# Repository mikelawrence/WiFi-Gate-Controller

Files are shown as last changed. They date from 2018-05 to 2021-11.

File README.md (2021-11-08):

# Wireless Gate Controller
After years of using weak garage door openers and trying to position them just right so my solar powered gate 400' away would open when needed I decided it was time to make a wireless controller of my own. 802.11 is a ubiquitous choice and with the right antenna range is not a problem. Two wireless modules consistently popped up when searching for low power embedded WiFi, ESP8266 and ATWINC1500. In the end I chose the ATWINC1500 module for it's compatibility with Arduino and it's low power modes. This board is fully compatible with the Arduino MRK1000 which includes a SAMD21G18 Arm processor and the ATWINC1500 module. I also chose to use MQTT. Recent projects showed how effective the MQTT client/server model is in this situation. I use Home Assistant for home automation and it directly supports MQTT.

This board is designed for and tested with a US Automation Gate Opener.

This PCB design uses my custom libraries available here [Mike's KiCad Libraries](https://github.com/mikelawrence/KiCad-Libraries).

This PCB was designed with [KiCad 5.1.2](http://kicad.org).

_Note: The LMZ21700 Simple Switcher, SAMD21G18 ARM Processor, and ATWINC1500 WiFi Module have exposed pads on the bottom which requires either a reflow oven or hot air to solder properly._

For Bill of Materials generation I use my version of [KiBoM](https://github.com/mikelawrence/KiBoM) forked from [SchrodingersGat](https://github.com/SchrodingersGat/KiBoM).

## Status
* Rev 1.1 PCB has been updated to support KiCad 5.1 libraries. Some footprints changed when libraries were updated but changes were minimal. This board has NOT been tested.
  * Order the PCB from [OSH Park](https://oshpark.com/shared_projects/2w66ZpSF).
  * Order the parts from Mouser using this [Shared BOM](https://www.mouser.com/ProjectManager/ProjectDetail.aspx?AccessID=595b0bc14b).
* Rev 1.0 PCB has been been ordered, assembled, and tested. Hardware is fully operational.
  * Order the PCB from [OSH Park](https://oshpark.com/shared_projects/rpQhhUss).
  * Order the parts from Mouser using this [Shared BOM](https://www.mouser.com/ProjectManager/ProjectDetail.aspx?AccessID=595b0bc14b).

## Board Preview
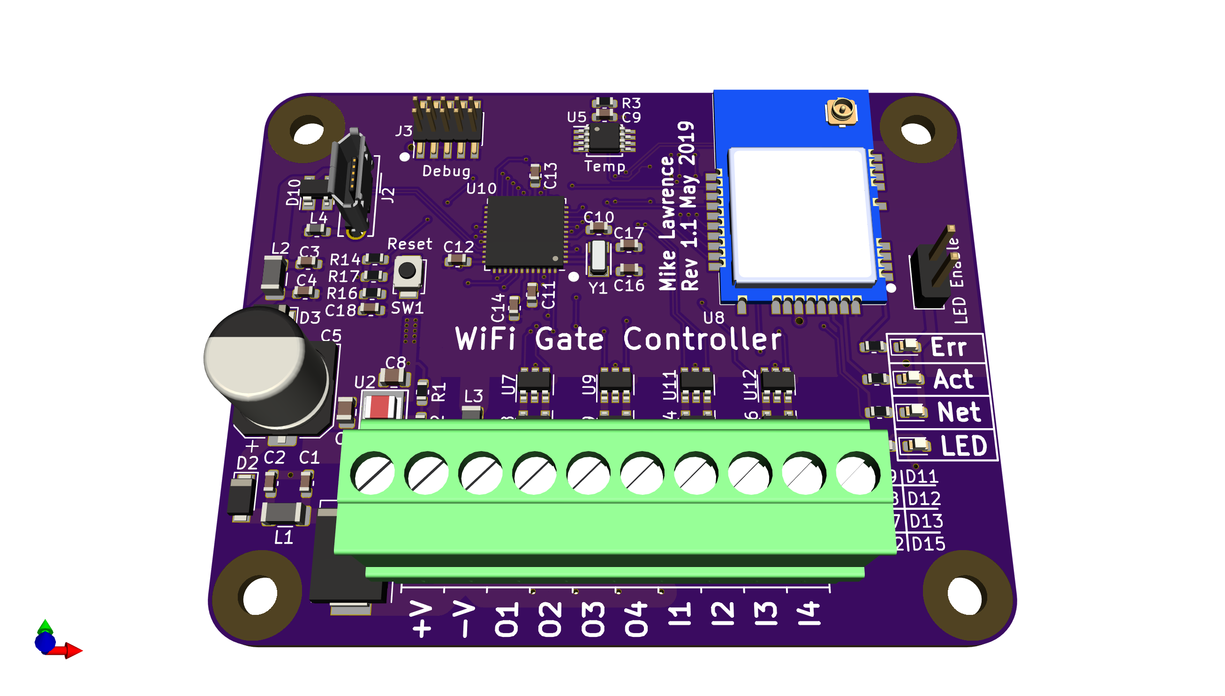
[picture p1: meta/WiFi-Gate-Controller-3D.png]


## Design
### Input Power
All components are powered by a 3.3VDC Simple Switcher from Texas Instruments (LMZ21700). Input power is 12VDC nominal with a range of 5V-17V. The with the switching power supply efficiency at about 80% the board current draws at the lowest 5mA and an average around 12mA. Peak current during transmit is about 100mA.

### Contact Inputs
Contact inputs use a simple pull-up to 5VDC and a Schmidt Trigger Inverter (SN74LVC2G14). Note: software debounce is still required. A high value pull-up resistor and series resistor (both 100k) were selected to reduce current levels when accidental high voltages are applied to the input. The resistor pull-ups should be installed where needed. If connecting to a gate controller that already has an input pulled up leave the pull-up resistors off. The inputs are 5V tolerant. ESD Protection devices are included to further protect the inputs. Due to the Schmidt Trigger Inverter the software sees a logic high when a contact is closed (shorted to -V).

### Contact Outputs
There are four contact outputs on the board which short to ground (-V) when activated. The switch is an overload protected Infineon Low-Side Automotive Switch (BTS3800SL). Each contact output has input circuitry identical to the contact inputs on the board. This allows detection of external contact closures for parallel wired contacts.

### SAMD ARM Processor and WiFi Module
The ARM processor and ATWINC1500 WiFi module are wired identical to the MKR1000 Arduino board, thus the Arduino development environment is used for software development and the ATWINC1500 module is directly supported.

## Setup
### Arduino Setup
This board is designed to mimic a [MKR1000](https://store.arduino.cc/usa/arduino-mkr1000) board from Arduino. Make sure the the MKR1000 board is supported by installing . Do this by opening the Board Manager as shown below.

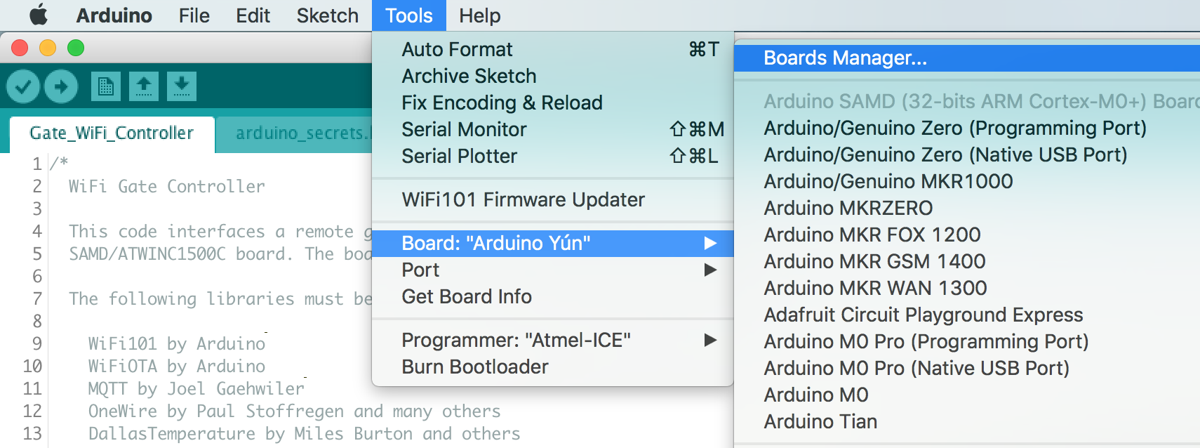
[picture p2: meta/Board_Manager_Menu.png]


Type in "samd" in the filter edit and you will see several options. Select "Arduino SAMD Boards (32-bits ARM Cortex-M0+)" and install the latest version as shown below.

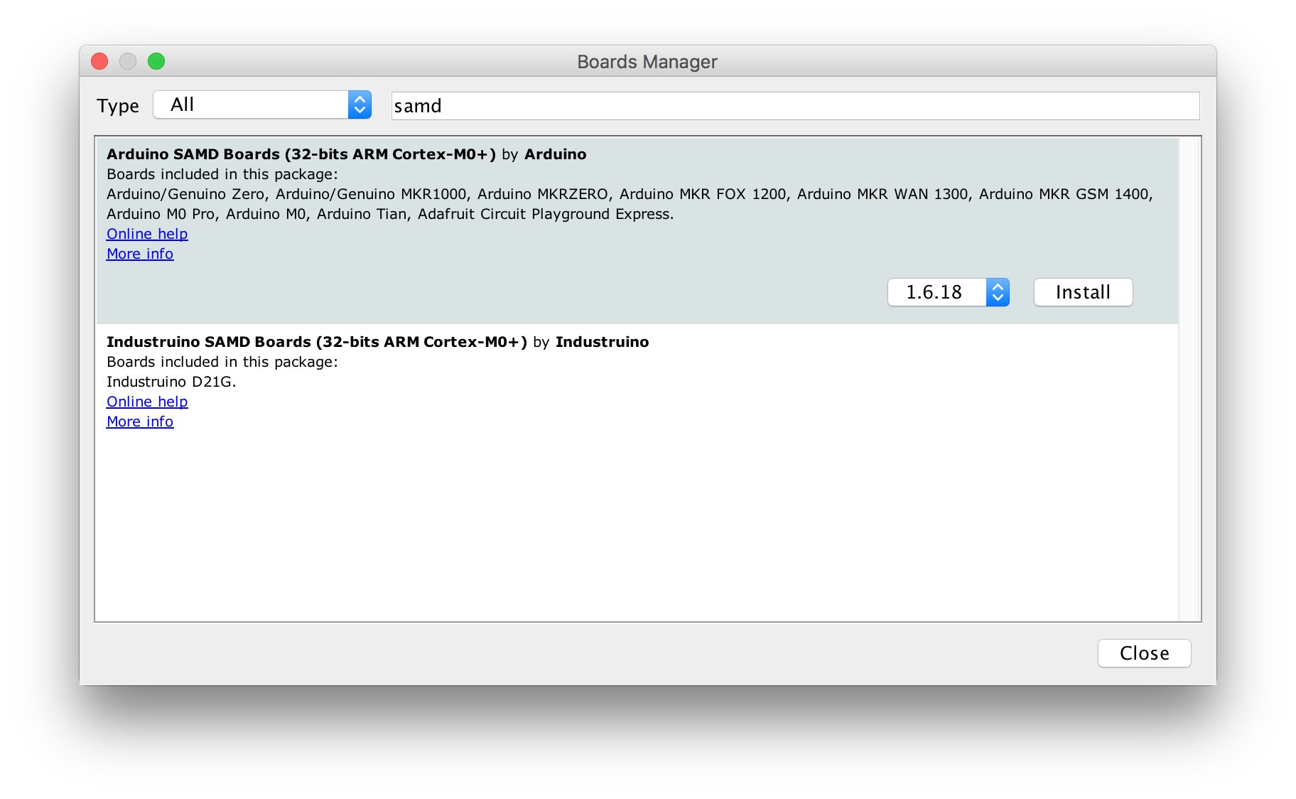
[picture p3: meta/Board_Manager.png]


It will take a few minutes to download and install the board package. Once complete it's time to install the necessary libraries. Start by opening the Library Manager as shown below.

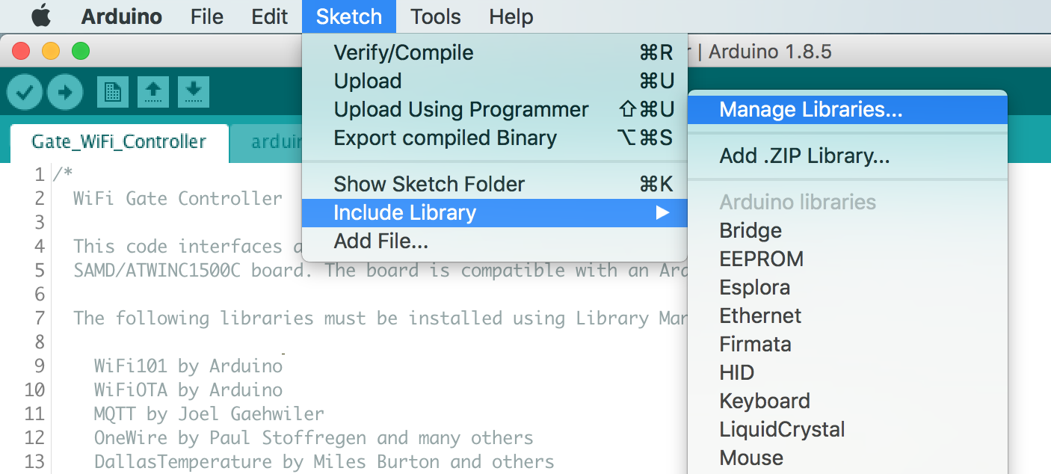
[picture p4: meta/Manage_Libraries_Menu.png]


Type in "mqtt" in the filter edit and scroll down until you see "MQTT by Joel Gaehwiler" as shown below.

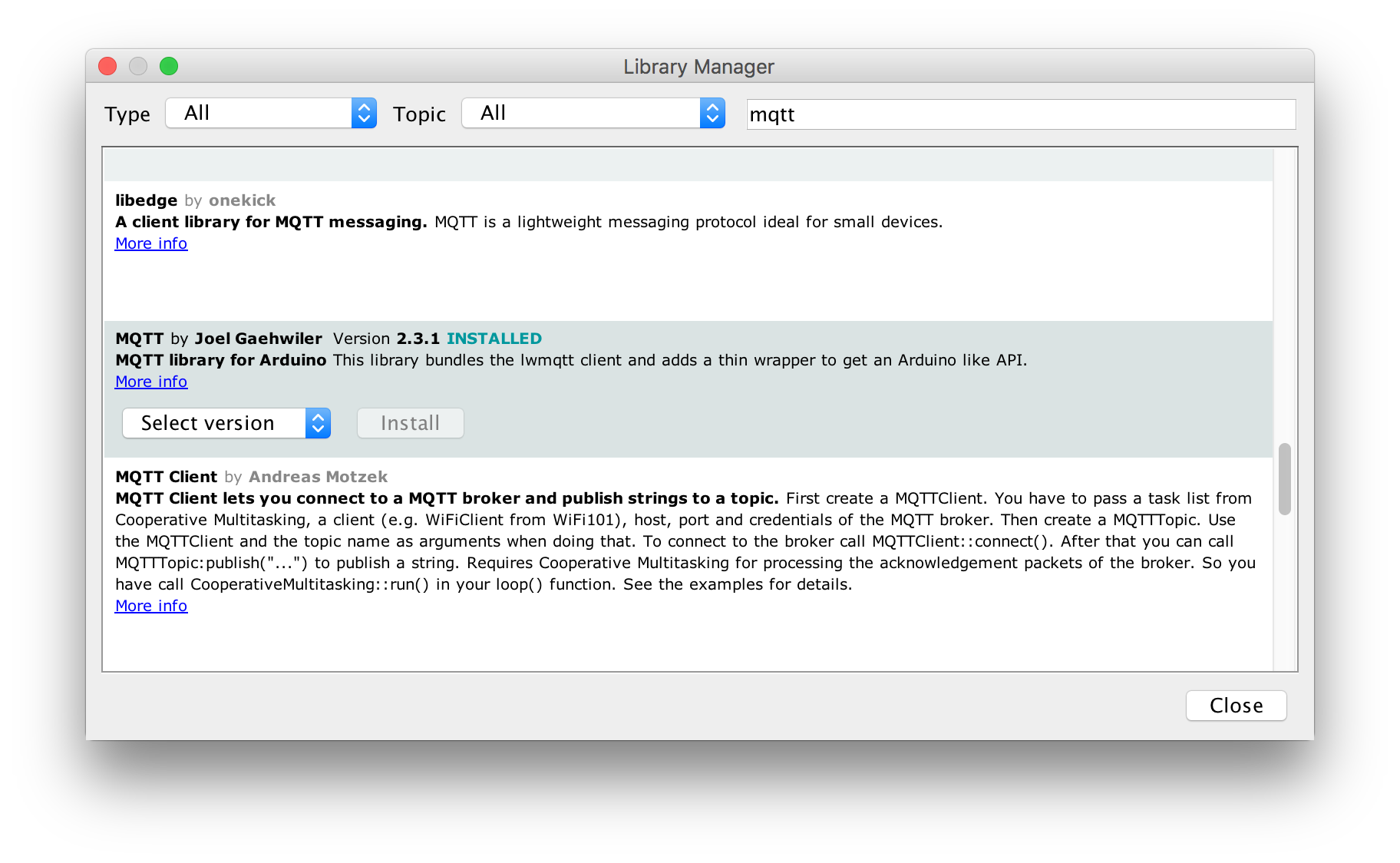
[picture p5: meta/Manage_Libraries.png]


Once "MQTT" is installed repeat the install for the following libraries.

* WiFi101 by Arduino
* WiFiOTA by Arduino
* OneWire by Paul Stoffregen and many others
* DallasTemperature by Miles Burton and others

### Board Setup
The Arduino development environment expects a bootloader in the SAMD ARM processor which will allow programming via USB. The bootloader must be programmed first using a supported programming pod. I used an "Atmel-ICE" pod but there are other options. First make sure you have selected the "Arduino/Genuino MKR1000" board as shown below.

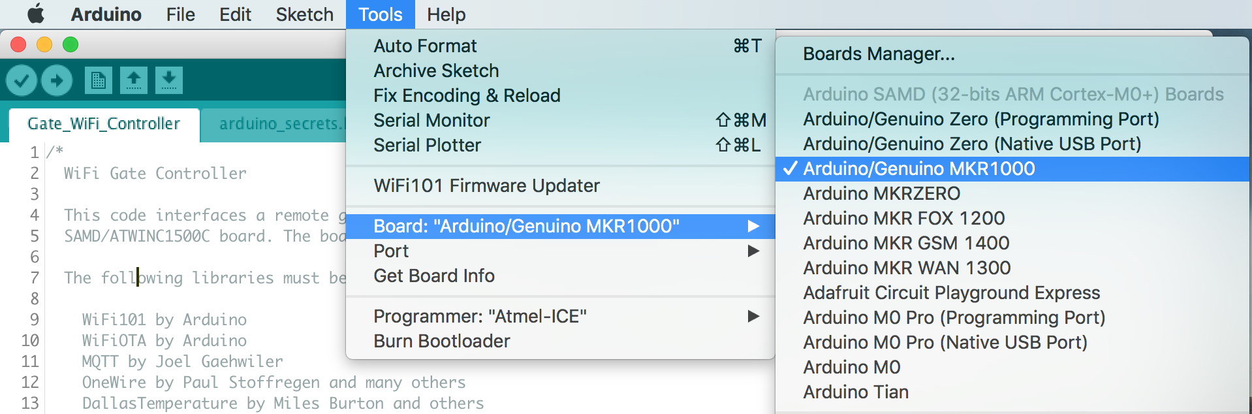
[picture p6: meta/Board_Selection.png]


Next select your programmer.

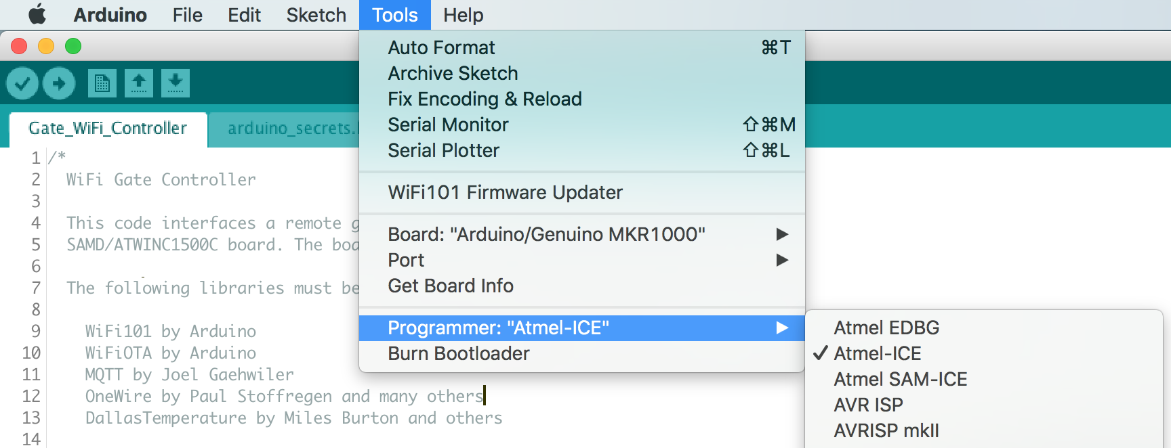
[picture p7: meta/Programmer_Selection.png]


Make sure the board is powered via USB and the programmer is connected to the debug connector then select "Burn Bootloader".

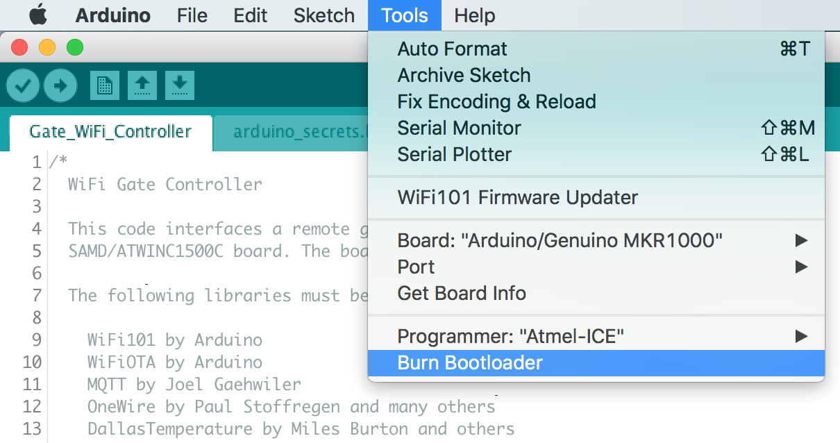
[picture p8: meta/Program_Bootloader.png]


Now the bootloader is programmed it's time to load the "WiFi101 FirmwareUpdater" example. This will update the firmware in the ATWINC1500 module.

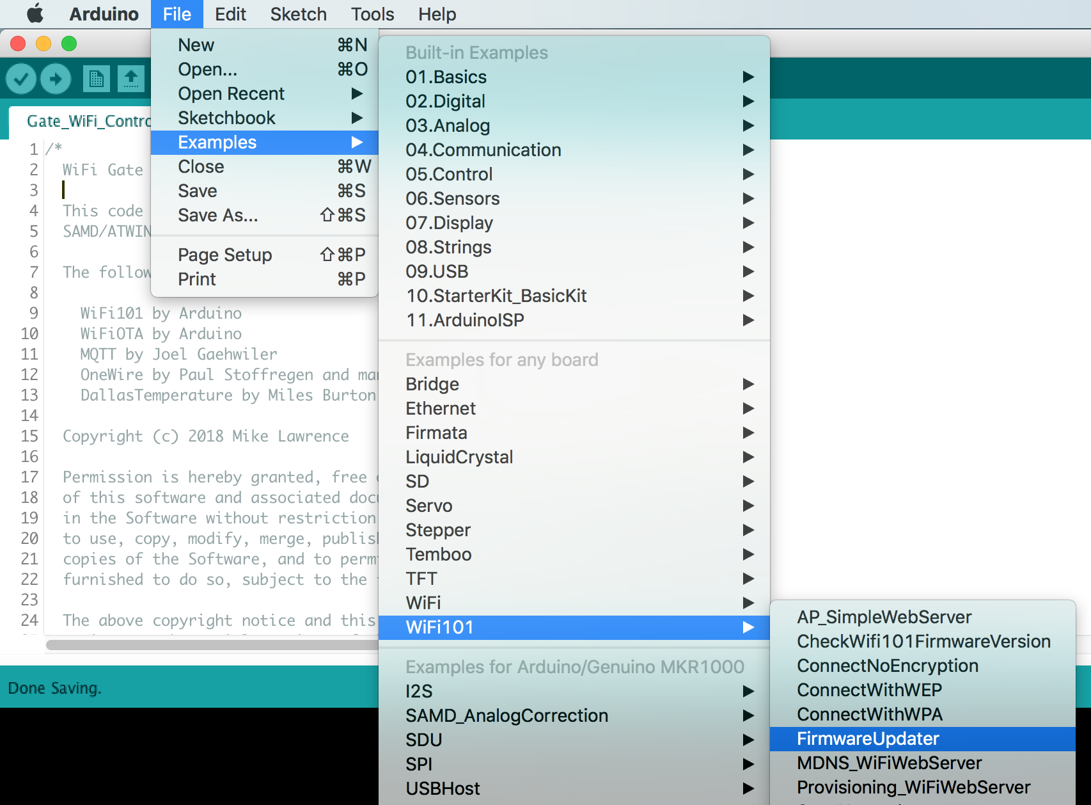
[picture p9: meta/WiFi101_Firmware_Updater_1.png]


Now "Upload" the "WiFi101 FirmwareUpdater" example.

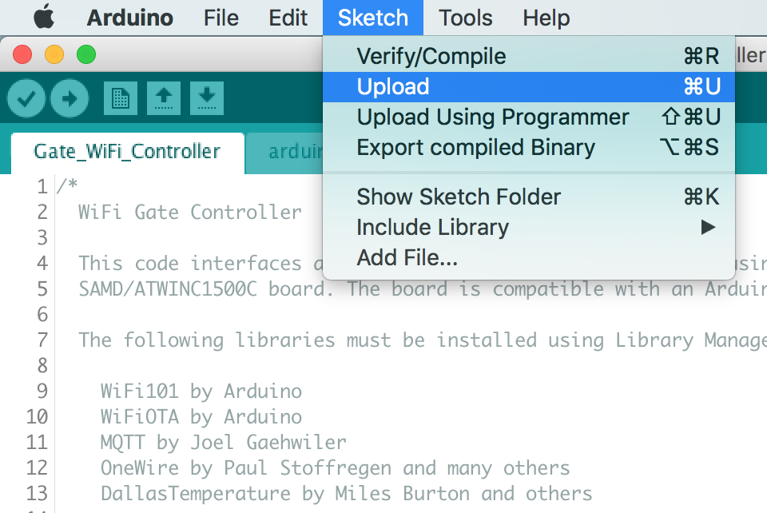
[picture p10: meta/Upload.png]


Update the ATWINC1500 module by selecting "WiFi101 Firmware Updater".

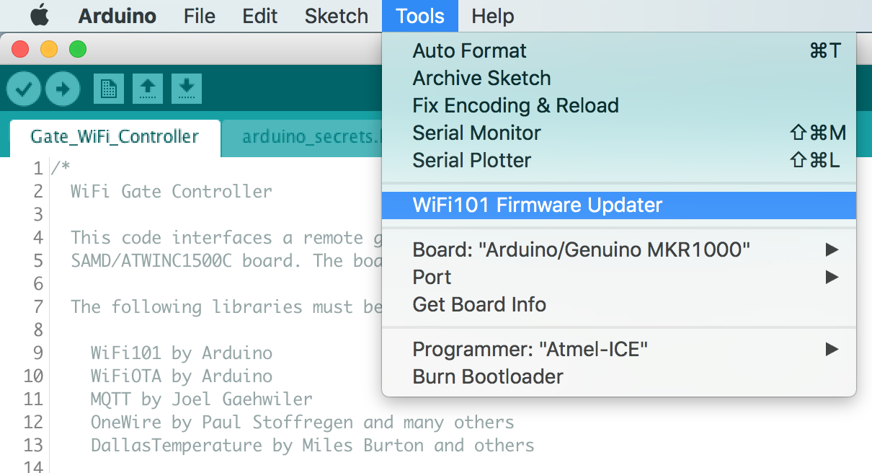
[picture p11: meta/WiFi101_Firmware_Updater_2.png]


Click the "Update Firmware" button.

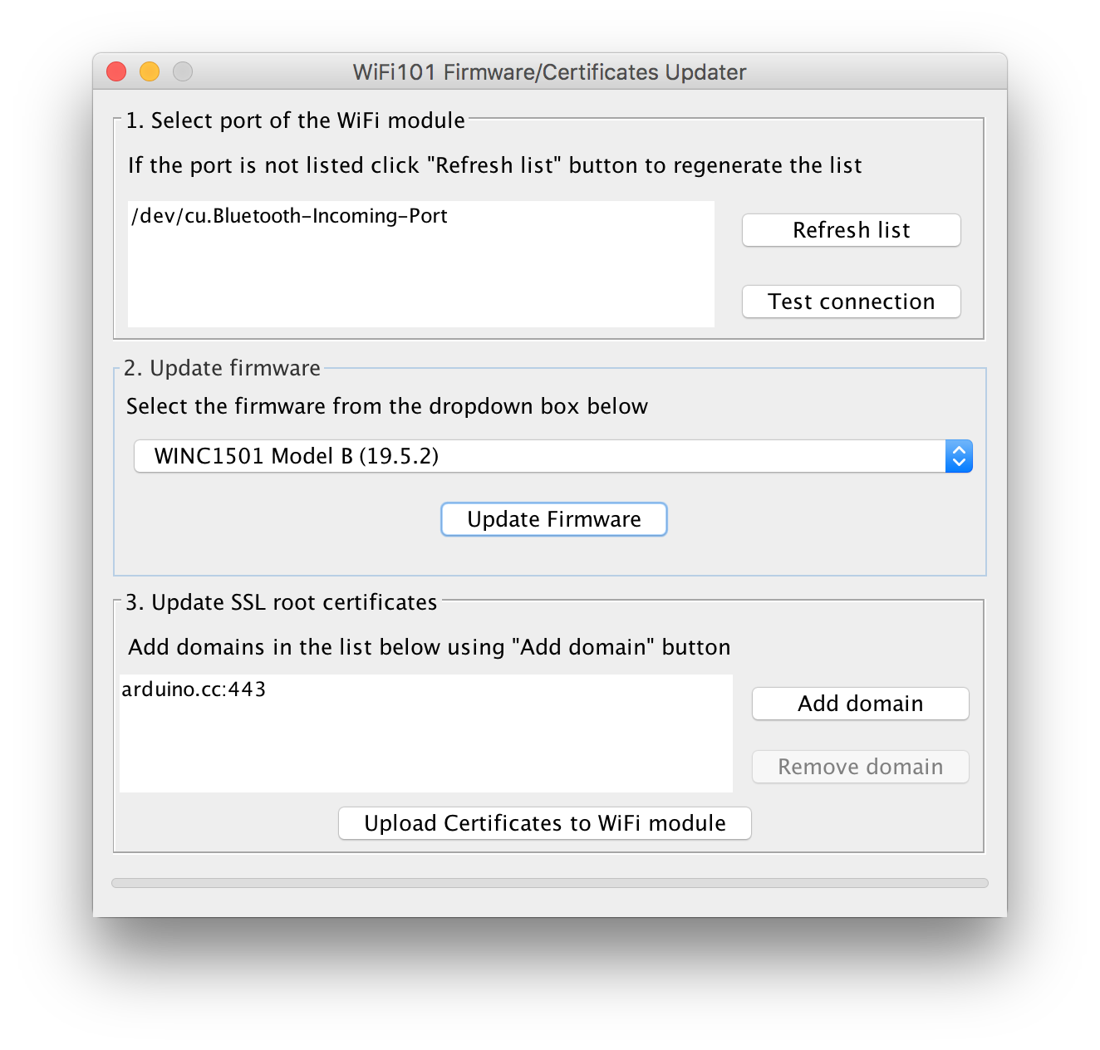
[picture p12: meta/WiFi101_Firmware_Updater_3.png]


Finally open the "WiFi_Gate_Controller.ino" sketch downloaded from GitHub. Update the necessary defines for your Wireless network and MQTT server settings see the [Code README](code/README.md) for more information. Now upload it just like the "WiFi101 FirmwareUpdater" example. All done!

# Acknowledgments
[Arduino](www.arduino.cc) kindly develops open source hardware and software which makes writing software for the board incredibly easy.

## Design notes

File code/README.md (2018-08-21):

# WiFi Gate Controller Sketch
The WiFi Gate Controller Sketch is written in C. It interfaces with a US Automation Gate Controller and will detect gate position and open/close the gate. The sketch is a discoverable cover and sensor for [Home Assistant](https://home-assistant.io/), an open-source home automation platform running on Python. [MQTT](http://mqtt.org/), a machine-to-machine (M2M)/"Internet of Things" connectivity protocol, is the basis of communication with Home Assistant.

## Status
This software is in the testing stage and is connected to my gate.
* This is now fixed. Using WiFi Low Power mode may have contributed to the problem. Experienced the controller going silent on the network (pump state machine continues to work correctly). It appears that the WiFi module can loose connection and still show the status as connected. Added MQTT connect timeout which stops the WiFi connection. This stop causes the WiFi reconnect and hopefully fix the problem automatically. Also turned off WiFi Low Power Mode.
* Home Assistant automatically detects all MQTT devices: Gate Cover, Temperature Sensor, RSSI Sensor, and Status Sensor.
* Control of the gate via MQTT works.
* Status reporting via MQTT works.

# Setup
## Sketch Setup
There are a few build defines that control how the sketch is built.

```c
/******************************************************************
 * Build defines
 ******************************************************************/
// Enable Watchdog Timer
#define ENABLE_WATCHDOG
// Enable OTA updates
//#define ENABLE_OTA_UPDATES
// Enable Serial on USB
//#define ENABLE_SERIAL
// Enable Low Power Mode on WiFi
#define ENABLE_WIFI_LOW_POWER
// Current Version
#define VERSION                   "0.1"
```

* When "ENABLE_WATCHDOG" is defined the Watchdog Timer is enabled with a 16 second timeout. This will reset the ARM processor is something goes bad.
* When "ENABLE_OTA_UPDATES" is defined the sketch can be updated using Arduino's Over-The-Air Update capability.
* When "ENABLE_SERIAL" is defined then status information is sent out the serial connection which in this case is the USB port. Otherwise the serial port won't even be enabled.
* When "ENABLE_WIFI_LOW_POWER" is defined the WINC1500 module is set to Low Power Mode. This can drop the current requirements of the module to a third or even less. Low Power Mode reduces the transmit frequency to the beacon interval and may also cause the module to hang occasionally.

The arduino_secrets.h file is not included on Github. You must create and edit it to meet your configuration.

```c
/******************************************************************
 * arduino_secrets.h
 ******************************************************************/
#define SECRET_SSID             "SSID of your WiFi network"
#define SECRET_PASSWORD         "Password for your WIFi network"
// IP address of MQTT server, host name may work but I've never tried
#define MQTT_SERVER             "192.168.0.230"
#define MQTT_SERVERPORT         1883
// MQTT user name and password leave as empty string if not used
#define MQTT_USERNAME           ""
#define MQTT_PASSWORD           ""
// Over-The-Air Update password if used
#define OTA_PASSWORD            "password"
```

The rest of the sketch settings are C defines in the [WiFi Gate Controller Sketch](WiFi_Gate_Controller/WiFi_Gate_Controller.ino).

```c
/******************************************************************
 * Application defines
 ******************************************************************/
// Name of this board, each board should be unique
// Used as MQTT Client ID, HASS Name, and OTA Name
#define BOARD_NAME                "Front Gate"
// input debounce time in milliseconds
#define DEBOUNCE_TIME             25
// output contact time in milliseconds
#define CONTACT_TIME              500
// output contact dead time between contact closures in milliseconds
#define CONTACT_DEADBAND_TIME     100
// temperature measurement time in milliseconds, Must be greater than 5 seconds
#define TEMP_RATE                 5*60*1000

/******************************************************************
 * Home Assistant MQTT Defines
 ******************************************************************/
#define HASS_PREFIX               "hass"
#define HASS_GATE_NAME            "front_gate"
```
* "BOARD_NAME" names the board so multiple instances of this board can on the WiFi network at the same time. It is used is several places including Home Assistant Name, OTA Name, and MQTT Client ID. This is a string.
* "DEBOUNCE_TIME" is how long to ignore contact changes on the input before accepting them as valid. This is an integer and the units are milliseconds.
* "CONTACT_TIME" is how long an output contact should be held active before being released. This is an integer and the units are milliseconds.
* "CONTACT_DEADBAND_TIME" is how long after a output contact has been released before another output contact may be activated. Any "OPEN" or "CLOSE" MQTT commands are ignored for CONTACT_TIME + CONTACT_DEADBAND_TIME milliseconds. This is an integer and the units are milliseconds.
* "TEMP_RATE" is how often the temperature should be sampled and updated via MQTT.  This is an integer and the units are milliseconds. The time must be greater than 5000 milliseconds.
* "HASS_PREFIX" is the Home Assistant MQTT Discovery Prefix as defined in your system. This is a string.
* "HASS_GATE_NAME" is used in the MQTT topics to identify the cover and sensor to Home Assistant. Home Assistant calls this the node id. It is a string and must not contain special characters including a space.

## Home Assistant Setup
The sketch is setup to enable MQTT Discovery on Home Assistant. If you don't want to use discovery here is the configuration of the gate in Home Assistant. Note the 'Front Gate' you see in the example yaml is the "BOARD_NAME" which is defined in [WiFi Gate Controller Sketch](WiFi_Gate_Controller/WiFi_Gate_Controller.ino) and 'front_gate' is "HASS_GATE_NAME". The WiFi Gate Controller uses the cover platform for Home Assistant ([MQTT Cover](https://www.home-assistant.io/components/cover.mqtt/)). The other sensors use the [MQTT Sensor](https://home-assistant.io/components/sensor.mqtt/) platform.

```yaml
# Example configuration.yaml entry
cover:
  # Front Gate cover
  - platform: mqtt_json
    name: "Front Gate"
    state_topic: "hass/cover/front_gate/gate/state"
    command_topic: "hass/cover/front_gate/gate/set"
    qos: 1
    retain: false

sensor:
  # Front Gate temperature
  - platform: mqtt
    name: "Front Gate Temperature"
    state_topic: "hass/cover/front_gate/temperature/state"
    unit_of_measurement: "°C"
  # Front Gate RSSI
  - platform: mqtt
    name: "Front Gate RSSI"
    state_topic: "hass/cover/front_gate/rssi/state"
    unit_of_measurement: "dBm"
  # Front Gate Status
  - platform: mqtt
    name: "Front Gate Status"
    state_topic: "hass/cover/front_gate/status/state"
```

Once the board is running Home Assistant should automatically pick up the cover and sensors with MQTT Discovery. Debugging Home Assistant problems is a bit of a stretch for this guide but here are a couple of hints.

* Make sure you have MQTT installed. If you use HASS.IO goto the HASS.IO configuration and install the Mosquitto Broker.
* Make sure you have MQTT discovery enabled. See [MQTT Discovery](https://home-assistant.io/docs/mqtt/discovery/).
* Make sure your MQTT discovery prefix matches the HASS_PREFIX in the [WiFi Gate Controller Sketch](WiFi_Gate_Controller/WiFi_Gate_Controller.ino).

I use HASS.IO with the Mosquitto Broker add-on installed and my configuration for MQTT is as follows...
```yaml
mqtt:
  broker: core-mosquitto
  discovery: true
  discovery_prefix: hass

```

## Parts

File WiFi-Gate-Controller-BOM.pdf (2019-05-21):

Quantity | References | Description | Manufacturer | Part Number | Vendor | Vendor Part Number
4 | C1 C2 C3 C4 | CAP, 0603, 1000pF, 10%, X7R, 10V | Vishay | VJ0603Y102KXAAC31 | Mouser | 77-VJ0603Y102KXAAC31
1 | C5 | CAP, SMD 8X10, 20%, EC, 35V | United Chemi-Con | EMVH350ADA101MHA0G | Mouser | 661-EMVH350ADA101M
3 | C6 C8 C19 | CAP, 0805, 22uf, 20%, X5R, 25V | Taiyo Yuden | TMK212BBJ226MG-TT | Mouser | 963-TMK212BBJ226MGTT
1 | C7 | CAP, 0603, 3300pF, 5%, X7R, 10V | Vishay | VJ0603Y332JXQPW1BC | Mouser | 77-VJ0603Y332JXQPBC
7 | C9 C10 C11 C12 C13 C15 C18 | CAP, 0603, 0.1uF, 20%, X7R, 10V | Vishay | VJ0603Y104JXQPW1BC | Mouser | 77-VJ0603Y104JXQPBC
2 | C14 C20 | CAP, 0603, 1uF, 10%, X7R, 10V | AVX | 0603ZC105JAT2A | Mouser | 581-0603ZC105JAT2A
2 | C16 C17 | CAP, 0603, 15pF, 5%, C0G, 50V | AVX | 06035A150JAT2A | Mouser | 581-06035A150J
4 | D1 D4 D5 D6 | TVS, SOT23, ESD Protection, CAN, 24V | ON Semiconductor | SZNUP2105LT1G | Mouser | 863-SZNUP2105LT1G
2 | D2 D3 | DIO, PowerDI123, Schottky Rectifier, 30V, 1A | Diodes Inc | DFLS130LQ | Mouser | 621-DFLS130L
1 | D7 | TVS, SMC, Transil, 1500W, 33V | ST Micro | SM15T33CA | Mouser | 511-SM15T33CA
5 | D8 D9 D14 D16 D17 | TVS, SOT23, ESD TVS Protection, Dual | Texas Instruments | TPD2E2U06QDBZRQ1 | Mouser | 595-TPD2E2U06QDBZRQ1
1 | D10 | TVS, SOT23, ESD Protection, USB | Nexperia | PRTR5V0U2X,215 | Mouser | 771-PRTR5V0U2X-T/R
1 | D11 | LED, 0603, Red | Lumex | SML-LX0603SRW-TR | Mouser | 696-SML-LX0603SRW
1 | D12 | LED, 0603, Yellow | Lumex | SML-LX0603SYW-TR | Mouser | 696-SML-LX0603SYW
1 | D13 | LED, 0603, Green | Lumex | SML-LX0603SGW-TR | Mouser | 696-SML-LX0603SGW
1 | D15 | LED, 0603, Orange | Lumex | SML-LX0603SOW-TR | Mouser | 696-SML-LX0603SOW
1 | J1 | CON, THT, Terminal Block, Pluggable, 3.5mm, 10 Pos | Phoenix | 1731565 | Mouser | 651-1731565
| J1 Mate | CON, THT, Terminal Block, Plug, 3.5mm, 10 Pos | Phoenix | 1862933 | Mouser | 651-1862933
1 | J2 | CON, THT, Micro USB 2.0 Type AB, Vertical | Wurth Electronics | 614105150721 | Mouser | 710-614105150621
1 | J3 | CON, SMD, 1.27mm Header, Dual Row, Vertical, 10 Pos | Amphenol FCI | 202112100010C4LF | Mouser | 649-202112100010C4LF
1 | JP1 | CON, THT, 2.54mm Header, Single Row, Vertical, 2 Pos | Molex | 22-03-2021 | Mouser | 538-22-03-2021
4 | L1 L2 L3 L5 | BEAD, 1206, 1k@100MHz, 2A | Murata | BLM31KN102SH1L | Mouser | 81-BLM31KN102SH1L
1 | L4 | BEAD, 0603, 470R@100MHz, 1A | Murata | BLM18PG471SN1D | Mouser | 81-BLM18PG471SN1D
1 | R1 | RES, 0603, 1.21M, 1%, T100 | Yageo | RC0603FR-071M21L | Mouser | 603-RC0603FR-071M21L
1 | R2 | RES, 0603, 383k, 1%, T100 | Panasonic | ERJ-3EKF3833V | Mouser | 667-ERJ-3EKF3833V
1 | R3 | RES, 0603, 4.7k, 1%, T100 | Panasonic | ERJ-3EKF4701V | Mouser | 667-ERJ-3EKF4701V
16 | R4 R5 R6 R10 R11 R13 R15 R18 R20 R21 R22 R23 R24 R25 R26 R27 | RES, 1206, 100k, 5%, T200 | Panasonic | ERJ-P08J104V | Mouser | 667-ERJ-P08J104V
4 | R7 R8 R9 R12 | RES, 0603, 1k, 1%, T100 | Panasonic | ERJ-3EKF1001V | Mouser | 667-ERJ-3EKF1001V
1 | R14 | RES, 0603, 39R, 1%, T100 | Panasonic | ERJ-3EKF39R0V | Mouser | 667-ERJ-3EKF39R0V
1 | R16 | RES, 0603, 10k, 1%, T100 | Panasonic | ERJ-3EKF1002V | Mouser | 667-ERJ-3EKF1002V
1 | R17 | RES, 0603, 330R, 1%, T100 | Panasonic | ERJ-3EKF3300V | Mouser | 667-ERJ-3EKF3300V
1 | SW1 | SW, SMD, Push Button | Omron | B3U-1000P | Mouser | 653-B3U-1000P
4 | U1 U3 U4 U6 | IC, SCT595, Smart Low Side Switch, 41V, 350mA | Infineon | BTS3800SL | Mouser | 726-BTS3800SL
1 | U2 | MODULE, SMD, Simple Switcher, 17V, 650mA | TI | LMZ21700SILR | Mouser | 595-LMZ21700SILR
1 | U5 | IC, MSOP8, 1-Wire Temperature Sensor | Maxim | DS18B20U+ | Mouser | 700-DS18B20U
4 | U7 U9 U11 U12 | IC, SOT23-6, Dual inverting Schmitt trigger | Texas Instruments | SN74LVC2G14DBVG4 | Mouser | 595-SN74LVC2G14DBVG4
1 | U8 | MODULE, SMD, WiFi, u.FL connector | Atmel | ATWINC1500-MR210UB1140 | Mouser | 579-C1500MR210UB1140
1 | U10 | IC, QFN44, MCU, ARM, 256kB Flash, 32kB SRAM, 48MHz | | ATSAMD21G18A-MUT | Mouser | 556-ATSAMD21G18A-MUT
1 | Y1 | XTL, SMD, 32.768kHz | Abracon | ABS07-32.768KHZ-9-T | Mouser | 815-ABS07-32.768K9T

# WiFi Gate Controller Rev 1.1

1

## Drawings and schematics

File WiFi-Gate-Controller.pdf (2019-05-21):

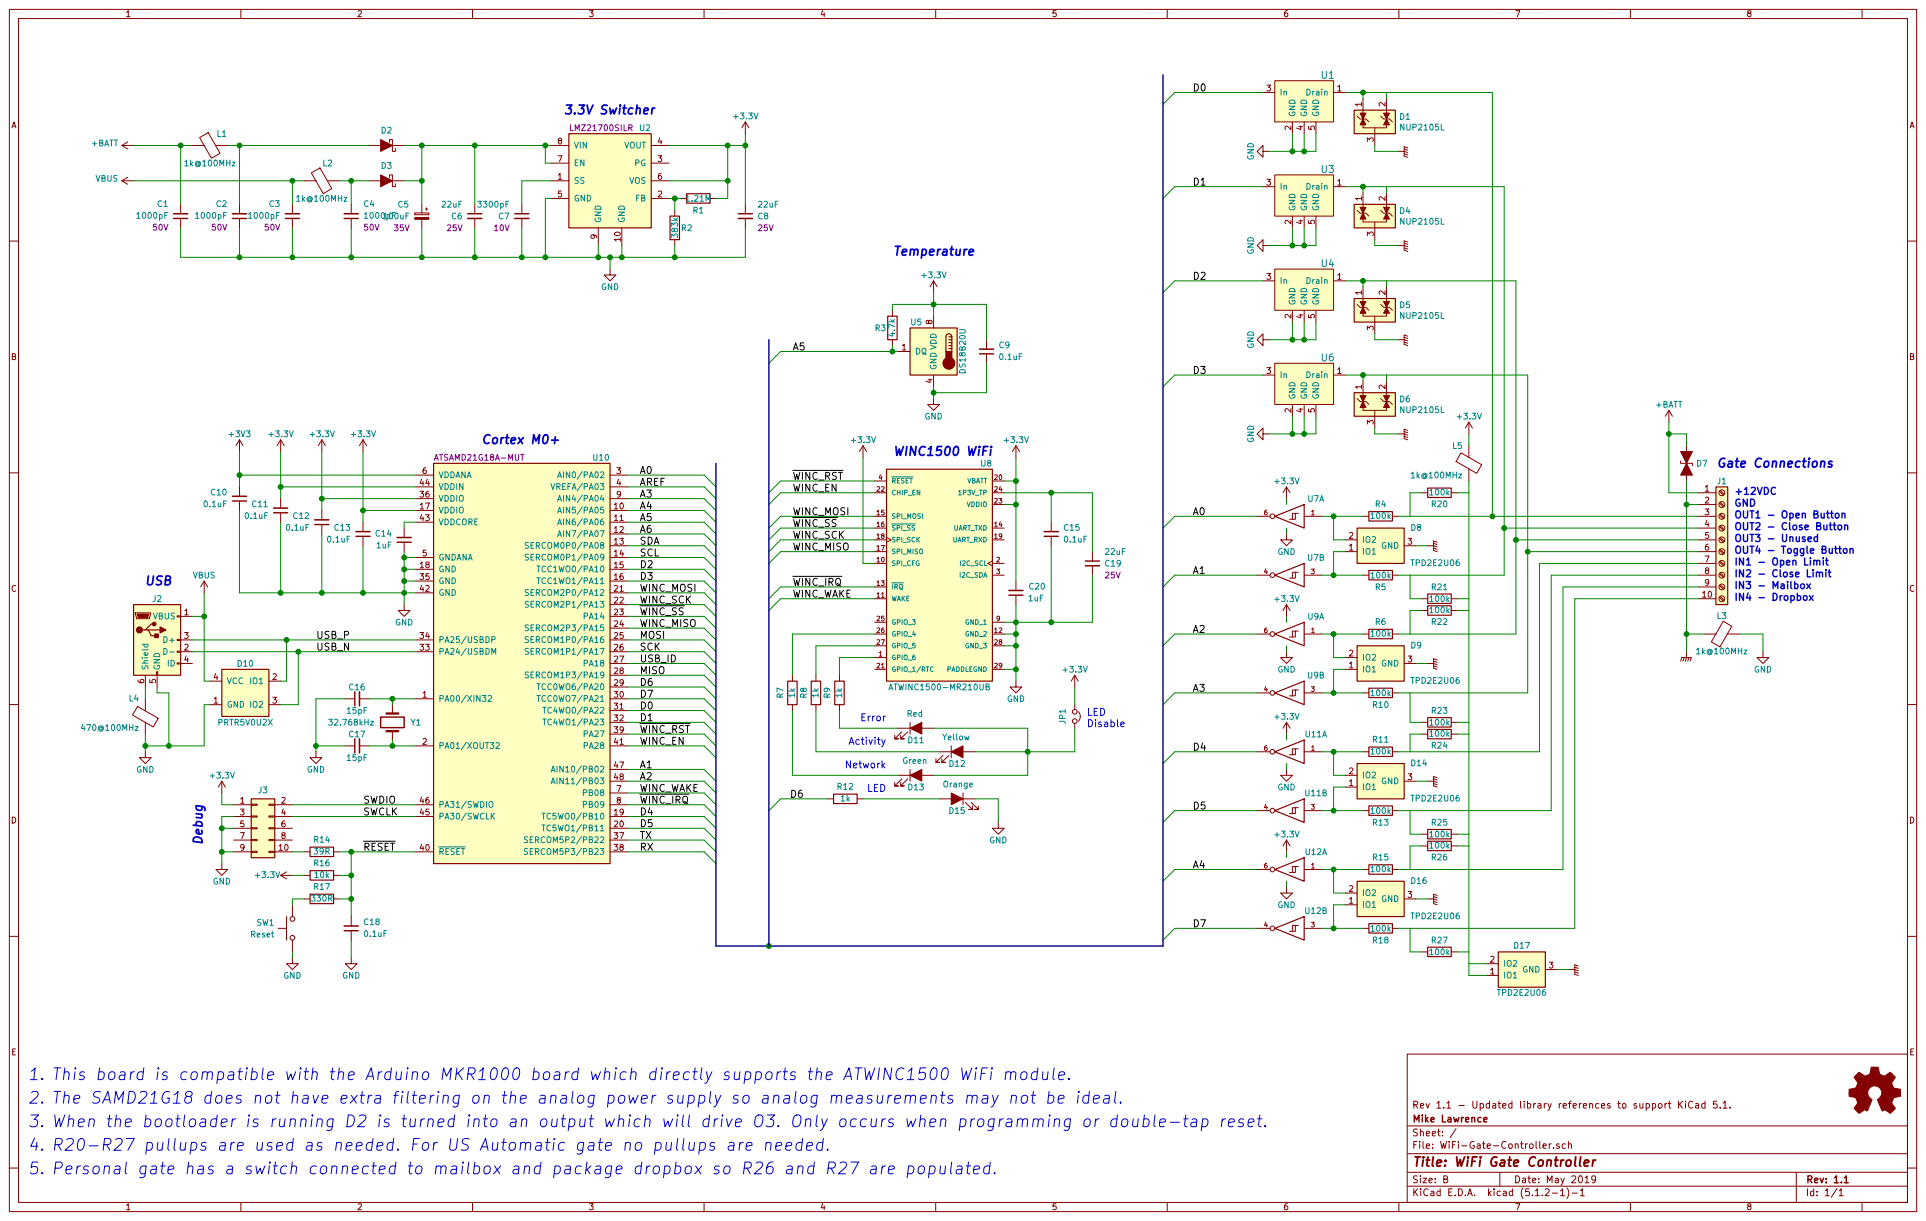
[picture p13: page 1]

1k@100MHz R20-R27 pullups are used as needed. For US Automatic gate no pullups are needed.

OUT2 - Close Button OUT3 - Unused OUT4 - Toggle Button GND

0.1uF 2. The SAMD21G18 does not have extra filtering on the analog power supply so analog measurements may not be ideal.

+3.3V GND GND GND GND

1uF GND 3. When the bootloader is running D2 is turned into an output which will drive O3. Only occurs when programming or double-tap reset.

SWCLK

WINC_IRQ

Id: 1/1 Title: WiFi Gate Controller File: WiFi-Gate-Controller.sch Sheet: / Mike Lawrence Rev 1.1 - Updated library references to support KiCad 5.1. GND

1. This board is compatible with the Arduino MKR1000 board which directly supports the ATWINC1500 WiFi module.

5. Personal gate has a switch connected to mailbox and package dropbox so R26 and R27 are populated.

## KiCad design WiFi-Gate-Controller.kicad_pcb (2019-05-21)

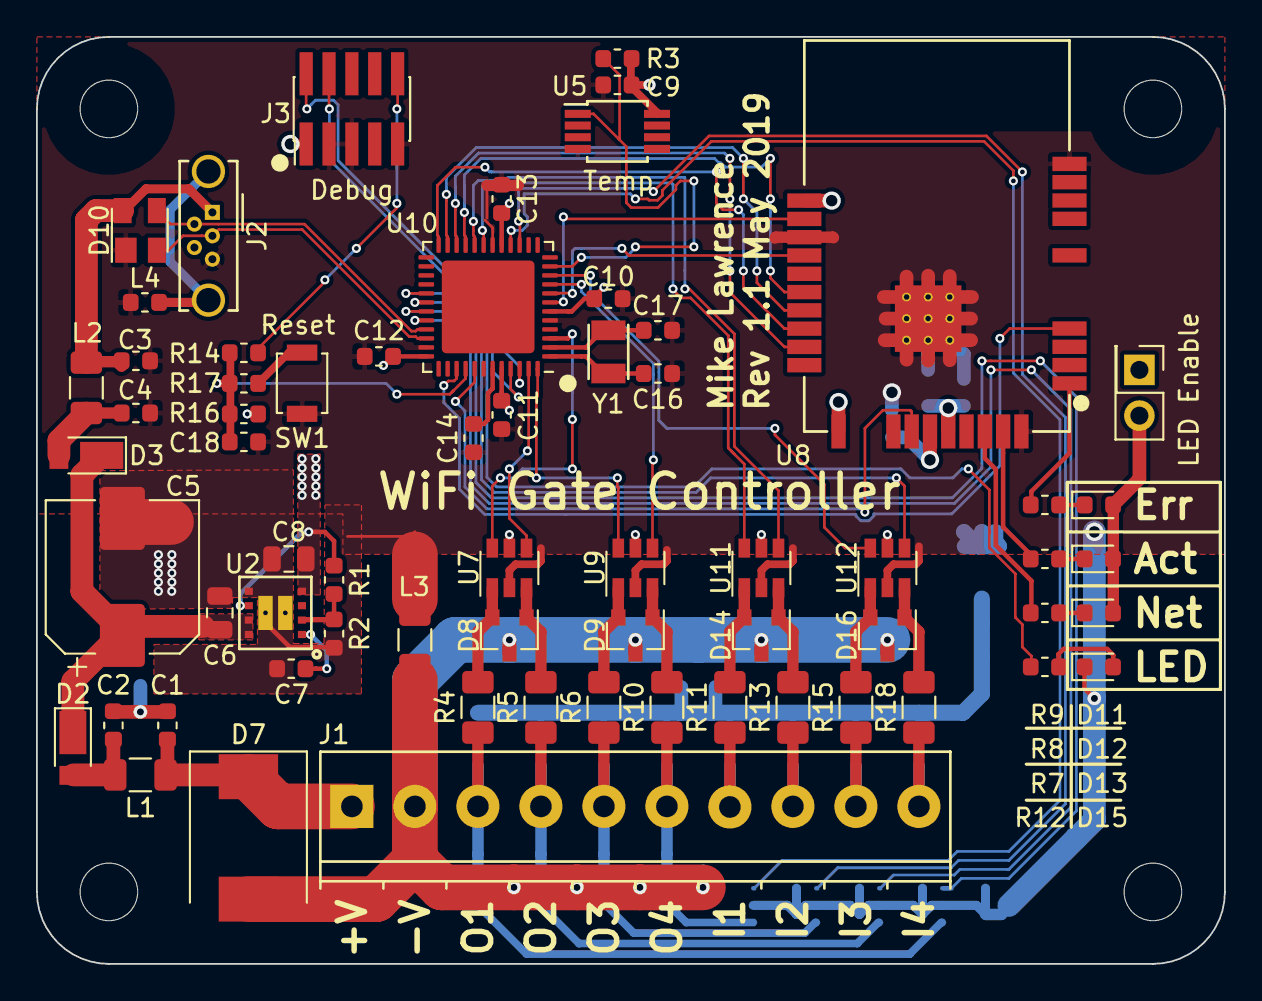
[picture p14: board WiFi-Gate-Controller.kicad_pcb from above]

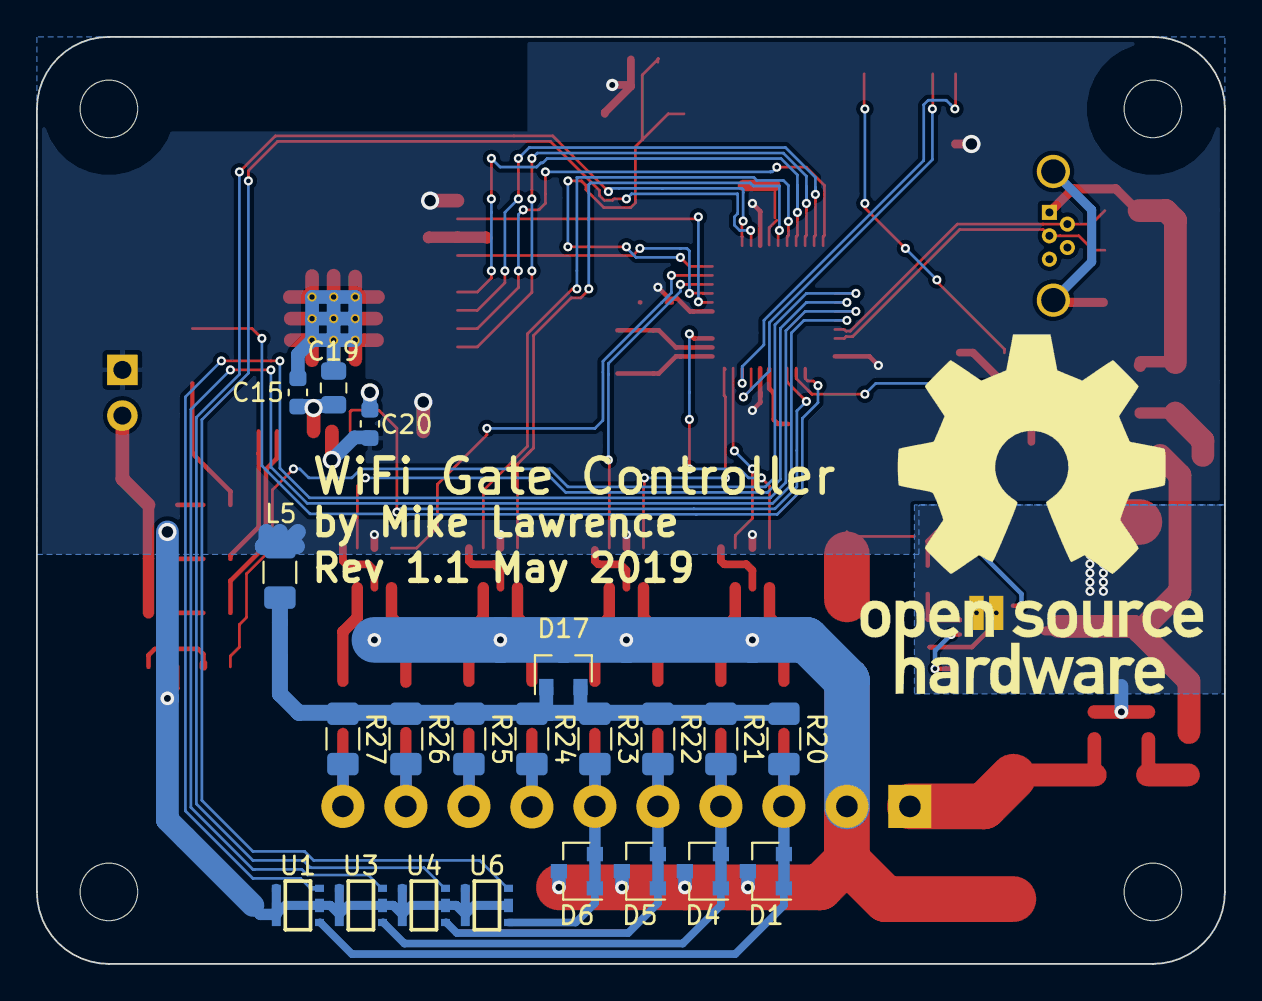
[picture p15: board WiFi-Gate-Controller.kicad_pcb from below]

Board: 2 copper layers, 66.0 x 51.5 mm, 86 parts (21 on the bottom side), 69 nets.

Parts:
C1, C2, C3, C4: 1000pF; C_0603_1608Metric
C5: 100uF; CP_Elec_8x10
C6, C8, C19: 22uF; C_0805_2012Metric
C7: 3300pF; C_0603_1608Metric
C9, C10, C11, C12, C13, C15, C18: 0.1uF; C_0603_1608Metric
C14, C20: 1uF; C_0603_1608Metric
C16, C17: 15pF; C_0603_1608Metric
D1, D4, D5, D6: NUP2105L; SOT-23
D2, D3: DFLS130; D_PowerDI-123
D7: SM15T33CA; D_SMC
D8, D9, D14, D16, D17: TPD2E2U06; SOT-23
D10: PRTR5V0U2X; SOT-143
D11: Red; LED_0603_1608Metric
D12: Yellow; LED_0603_1608Metric
D13: Green; LED_0603_1608Metric
D15: Orange; LED_0603_1608Metric
J1: Screw_Terminal_01x10; TerminalBlock_Phoenix_PT-3.5mm_10pol
J2: USB_B_Micro; USB_Micro-B_Wuerth_614105150721_Vertical_CircularHoles
J3: Cortex Debug; PinHeader_2x05_P1.27mm_Vertical_SMD
JP1: LED Disable; PinHeader_2x01_P2.54mm_Vertical
L1, L2, L3, L5: 1k@100MHz; L_1206_3216Metric
L4: 470@100MHz; L_0603_1608Metric
R1: 1.21M; R_0603_1608Metric
R2: 383k; R_0603_1608Metric
R3: 4.7k; R_0603_1608Metric
R4, R5, R6, R10, R11, R13, R15, R18, R20, R21, R22, R23, R24, R25, R26, R27: 100k; R_1206_3216Metric
R7, R8, R9, R12: 1k; R_0603_1608Metric
R14: 39R; R_0603_1608Metric
R16: 10k; R_0603_1608Metric
R17: 330R; R_0603_1608Metric
SW1: Reset; SW_SPST_B3U-1000P
U1, U3, U4, U6: BTS3800SL; Infineon_PG-SCT595-5-1
U2: LMZ21700; Converter_DCDC_Texas-SIL0008E
U5: DS18B20U; MSOP-8_3x3mm_P0.65mm
U7, U9, U11, U12: 74LVC2G14; SOT-23-6
U8: ATWINC1500-MR210UB; Microchip_ATWINC1500-MR210UB
U10: SAMD21G18-M; QFN-48-1EP_7x7mm_P0.5mm_EP5.15x5.15mm
Y1: 32.768kHz; Crystal_SMD_Abracon_ABS07-2Pin_3.2x1.5mm

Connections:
+3V3: C8.1, C9.2, C10.2, C11.2, C12.2, C13.2, C20.2, J3.1, JP1.1, L5.1, R1.1, R3.1, R16.2, U2.4, U2.6, U5.8, U7.5, U8.10, U8.20, U8.23, U9.5, U10.6, U10.17, U10.36, U10.44, U11.5, U12.5
+BATT: C1.2, D7.1, J1.1, L1.1
/A0: U7.6, U10.3
/A1: U7.4, U10.47
/A2: U9.6, U10.48
/A3: U9.4, U10.9
/A4: U10.10, U12.6
/A5: R3.2, U5.1, U10.11
/D0: U1.3, U10.31
/D1: U3.3, U10.32
/D2: U4.3, U10.15
/D3: U6.3, U10.16
/D4: U10.19, U11.6
/D5: U10.20, U11.4
/D6: R12.1, U10.29
/D7: U10.30, U12.4
/SWCLK: J3.4, U10.45
/SWDIO: J3.2, U10.46
/USB_N: D10.3, J2.2, U10.33
/USB_P: D10.2, J2.3, U10.34
/WINC_EN: U8.22, U10.41
/WINC_MISO: U8.17, U10.24
/WINC_MOSI: U8.15, U10.21
/WINC_SCK: U8.18, U10.22
/WINC_WAKE: U8.11, U10.7
/~RESET~: C18.2, R14.1, R16.1, R17.1, U10.40
/~WINC_IRQ: U8.13, U10.8
/~WINC_RST: U8.4, U10.39
/~WINC_SS: U8.16, U10.23
GND: C1.1, C2.1, C3.1, C4.1, C5.2, C6.2, C7.2, C8.2, C9.1, C10.1, C11.1, C12.1, C13.1, C14.1, C15.1, C16.1, C17.1, C18.1, C19.2, C20.1, D10.1, D15.1, J2.5, J3.3, J3.5, J3.9, L3.2, L4.1, R2.2, SW1.2, U1.2, U1.4, U1.5, U2.5, U2.9, U2.10, U3.2, U3.4, U3.5, U4.2, U4.4, U4.5, U5.4, U6.2, U6.4, U6.5, U7.2, U8.9, U8.12, U8.28, U8.29, U9.2, U10.5, U10.18, U10.35, U10.42, U11.2, U12.2
GNDPWR: D1.3, D4.3, D5.3, D6.3, D7.2, D8.3, D9.3, D14.3, D16.3, D17.3, J1.2, L3.1
unnamed: C2.2, D2.2, L1.2
unnamed: C4.2, D3.2, L2.2
unnamed: C5.1, C6.1, D2.1, D3.1, U2.7, U2.8
unnamed: C7.1, U2.1
unnamed: C14.2, U10.43
unnamed: C15.2, C19.1, U8.24
unnamed: C16.2, U10.1, Y1.1
unnamed: C17.2, U10.2, Y1.2
unnamed: D1.1, D1.2, J1.3, R4.1, R20.2, U1.1
unnamed: D4.1, D4.2, J1.4, R5.1, R21.2, U3.1
unnamed: D5.1, D5.2, J1.5, R6.1, R22.2, U4.1
unnamed: D6.1, D6.2, J1.6, R10.1, R23.2, U6.1
unnamed: D8.1, R5.2, U7.3
unnamed: D8.2, R4.2, U7.1
unnamed: D9.1, R10.2, U9.3
unnamed: D9.2, R6.2, U9.1
unnamed: D11.1, R9.2
unnamed: D11.2, D12.2, D13.2, JP1.2
unnamed: D12.1, R8.2
unnamed: D13.1, R7.2
unnamed: D14.1, R13.2, U11.3
unnamed: D14.2, R11.2, U11.1
unnamed: D15.2, R12.2
unnamed: D16.1, R18.2, U12.3
unnamed: D16.2, R15.2, U12.1
unnamed: D17.1, D17.2, L5.2, R20.1, R21.1, R22.1, R23.1, R24.1, R25.1, R26.1, R27.1
unnamed: J1.7, R11.1, R24.2
unnamed: J1.8, R13.1, R25.2
unnamed: J1.9, R15.1, R26.2
unnamed: J1.10, R18.1, R27.2
unnamed: J2.6, L4.2
unnamed: J3.10, R14.2
unnamed: R1.2, R2.1, U2.2
unnamed: R7.1, U8.26
unnamed: R8.1, U8.27
unnamed: R9.1, U8.1
unnamed: R17.2, SW1.1
VBUS: C3.2, D10.4, J2.1, L2.1

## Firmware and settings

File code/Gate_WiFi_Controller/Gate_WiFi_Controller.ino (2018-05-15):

/*
  WiFi Gate Controller 
  
  This code interfaces a remote gate opener (US Automation) using a custom 
  SAMD/ATWINC1500C board. The board is compatible with an Arduino MKR1000.

  The following libraries must be installed using Library Manager:
  
    WiFi101 by Arduino
    WiFiOTA by Arduino
    MQTT by Joel Gaehwiler
    OneWire by Paul Stoffregen and many others
    DallasTemperature by Miles Burton and others
  
  Copyright (c) 2018 Mike Lawrence

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
  THE SOFTWARE IS PROVIDED "AS IS", WITHOUT WARRANTY OF ANY KIND, EXPRESS OR
  IMPLIED, INCLUDING BUT NOT LIMITED TO THE WARRANTIES OF MERCHANTABILITY,
  FITNESS FOR A PARTICULAR PURPOSE AND NONINFRINGEMENT. IN NO EVENT SHALL THE
  AUTHORS OR COPYRIGHT HOLDERS BE LIABLE FOR ANY CLAIM, DAMAGES OR OTHER
  LIABILITY, WHETHER IN AN ACTION OF CONTRACT, TORT OR OTHERWISE, ARISING FROM,
  OUT OF OR IN CONNECTION WITH THE SOFTWARE OR THE USE OR OTHER DEALINGS IN THE
  SOFTWARE.
*/
// Modify ../WiFi101/src/bsp/include/nm_bsp_internal.h library file
// so that CONF_PERIPH is defined. This will enabled LEDS from WiFi Module
#include <WiFi101.h>
#include <WiFi101OTA.h>
#include <MQTT.h>
#include <OneWire.h> 
#include <DallasTemperature.h>
#include <avr/dtostrf.h>
#include "arduino_secrets.h"
/******************************************************************
 * Definitions in arduino_secrets.h
 ******************************************************************/
/*
#define SECRET_SSID             "SSID of your WiFi network"
#define SECRET_PASSWORD         "Password for your WIFi network"
// IP address of MQTT server, host name may work but I've never tried
#define MQTT_SERVER             "192.168.0.230"
#define MQTT_SERVERPORT         1883
// MQTT user name and password leave as empty string if not used
#define MQTT_USERNAME           ""
#define MQTT_PASSWORD           ""
// Over-The-Air Update password if used
#define OTA_PASSWORD            "password"
*/

/******************************************************************
 * Build defines
 ******************************************************************/
// Enable Watchdog Timer
#define ENABLE_WATCHDOG
// Enable OTA updates
//#define ENABLE_OTA_UPDATES
// Enable Serial on USB
//#define ENABLE_SERIAL
// Current Version
#define VERSION                   "0.1"

/******************************************************************
 * Application defines
 ******************************************************************/
// Name of this board, each board should be unique
// Used as MQTT Client ID, HASS Name, and OTA Name
#define BOARD_NAME                "Front Gate"
// input debounce time in milliseconds
#define DEBOUNCE_TIME             25
// output contact time in milliseconds
#define CONTACT_TIME              500
// output contact dead time between contact closures in milliseconds
#define CONTACT_DEADBAND_TIME     100
// temperature measurement time in milliseconds, Must be greater than 5 seconds
#define TEMP_RATE                 5*60*1000

/******************************************************************
 * Home Assistant MQTT Defines
 ******************************************************************/
#define HASS_PREFIX               "hass"
#define HASS_GATE_NAME            "front_gate"
// HASS defines below here should not be modified
#define HASS_GATE_CONFIG_TOPIC    HASS_PREFIX "/cover/" HASS_GATE_NAME "/gate/config"
#define HASS_GATE_STATE_TOPIC     HASS_PREFIX "/cover/" HASS_GATE_NAME "/gate/state"
#define HASS_GATE_COMMAND_TOPIC   HASS_PREFIX "/cover/" HASS_GATE_NAME "/gate/set"
#define HASS_GATE_CONFIG          "{ \"name\": \"" BOARD_NAME "\", \"command_topic\": \"" HASS_GATE_COMMAND_TOPIC \
                                  "\", \"state_topic\": \"" HASS_GATE_STATE_TOPIC "\", \"qos\": 1, \"retain\": false }"
#define HASS_TEMP_CONFIG_TOPIC    HASS_PREFIX "/sensor/" HASS_GATE_NAME "/temperature/config"
#define HASS_TEMP_STATE_TOPIC     HASS_PREFIX "/sensor/" HASS_GATE_NAME "/temperature/state"
#define HASS_TEMP_CONFIG          "{ \"name\": \"" BOARD_NAME " Temperature\", \"state_topic\": \"" HASS_TEMP_STATE_TOPIC \
                                  "\", \"unit_of_measurement\": \"°C\" }"
#define HASS_RSSI_CONFIG_TOPIC    HASS_PREFIX "/sensor/" HASS_GATE_NAME "/rssi/config"
#define HASS_RSSI_STATE_TOPIC     HASS_PREFIX "/sensor/" HASS_GATE_NAME "/rssi/state"
#define HASS_RSSI_CONFIG          "{ \"name\": \"" BOARD_NAME " RSSI\", \"state_topic\": \"" HASS_RSSI_STATE_TOPIC \
                                  "\", \"unit_of_measurement\": \"dBm\" }"
#define HASS_STATUS_CONFIG_TOPIC  HASS_PREFIX "/sensor/" HASS_GATE_NAME "/status/config"
#define HASS_STATUS_STATE_TOPIC   HASS_PREFIX "/sensor/" HASS_GATE_NAME "/status/state"
#define HASS_STATUS_CONFIG        "{ \"name\": \"" BOARD_NAME " Status\", \"state_topic\": \"" HASS_STATUS_STATE_TOPIC "\" }"

/******************************************************************
 * Board Defines
 ******************************************************************/
// Output defines
#define NUMBER_OUTPUTS          4
#define OPEN_BUTTON             0
#define CLOSE_BUTTON            1
#define TOGGLE_BUTTON           2
#define UNUSED_BUTTON           3
// Input defines
#define NUMBER_INPUTS           8
#define OPEN_BUTTON_SENSE       0
#define CLOSE_BUTTON_SENSE      1
#define UNUSED_BUTTON_SENSE     2
#define TOGGLE_BUTTON_SENSE     3
#define OPEN_LIMIT_SENSE        4
#define CLOSE_LIMIT_SENSE       5
#define MAILBOX_SENSE           6
#define DROPBOX_SENSE           7
// LED
#define BOARD_LED               LED_BUILTIN
// pin number array for the four outputs on this board (pins are D0, D1, D2, D3)
const int8_t output_pins[NUMBER_OUTPUTS] = {0, 1, 2, 3};
// pin number array for the eight inputs on this board (pins are A0, A1, A2, A3, D4, D5, A4, D7)
const int8_t input_pins[NUMBER_INPUTS] = {PIN_A0, PIN_A1, PIN_A2, PIN_A3, 4, 5, PIN_A4, 7};
// Enumeration for gate state which also keeps track of gate opening or closing
enum GateStateEnum {GS_UNKNOWN, GS_RESET, GS_ERROR, GS_CLOSED, GS_OPEN, GS_CLOSING, GS_OPENING}; 

/******************************************************************
 * Global Variables
 ******************************************************************/
// Network
WiFiClient net;
// MQTT CLient
MQTTClient mqtt(1024);
// oneWire instance to communicate with any 1-Wire devices  
OneWire oneWire(PIN_A5); 
// Dallas Temperature measurement . 
DallasTemperature sensors(&oneWire);

// used to keep track of time to keep outputs active
uint32_t lastOutputTime[NUMBER_OUTPUTS] = {0, 0, 0, 0};
// current output state, arranged in array by input_pins
uint8_t  outputState[NUMBER_OUTPUTS] = {LOW, LOW, LOW, LOW};
// output in progress including deadband bewteen contact closures
uint8_t  outputDeadband = HIGH;
// used to keep track of deadband time between concact closures
uint32_t lastOutputDeadbandTime = 0;
// current input state, arranged in array by input_pins
uint8_t  inputState[NUMBER_INPUTS] = {-1, -1, -1, -1, -1, -1, -1, -1};
// last Gate open/closed state true/false
int8_t   lastGateOpenState = -1;
// when true a reset occurred recently
bool     resetOccurred = true;
// when true WiFi was recently disconnected from the network
bool     wifiDisconnectOccurred = true;
// when true WiFi was recently connected to the network
bool     wifiConnectOccurred = false;

// Arduino setup function
void setup() {
  // Serial setup
  #ifdef ENABLE_SERIAL
  //while (!Serial);                                  // wait until serial monitor is open
  Serial.begin(115200);
  #endif
  
  // configure LED output
  pinMode(BOARD_LED, OUTPUT);
  digitalWrite(BOARD_LED, LOW);                       // LED pin is an output and currently off
  
  // configure outputs
  for (int i = 0; i < NUMBER_OUTPUTS; i++) {
    pinMode(output_pins[i], OUTPUT);                  // set mode to output
    digitalWrite(output_pins[i], LOW);                // set output to LOW
  }
  
  // configure inputs (all active high, all push/pull driven)
  for (int i = 0; i < NUMBER_INPUTS; i++) {
    pinMode(input_pins[i], INPUT);                    // set mode to input
  }
  
  // takes a bit for the USB to come up
  #ifdef ENABLE_SERIAL
  delay(2000);
  #endif
  
  // Announce who we are and software
  #ifdef ENABLE_SERIAL
  Serial.println("\nWiFi Gate Controller: " BOARD_NAME);
  Serial.println("  Software Version: " VERSION);
  #endif
  
  // Start up the Dallas Temperature library 
  sensors.begin();
  // see that we have at least one temperature sensor
  #ifdef ENABLE_SERIAL
  if (sensors.getDeviceCount() == 0) {
      Serial.println("No 1-Wire temperature sensors found.");
  } else {
    DeviceAddress deviceAddress;
    sensors.getAddress(deviceAddress, 0);
    Serial.print("Found ");
    switch (deviceAddress[0]) {
      case 0x10:
        Serial.print("DS18S20");
        break;
      case 0x28:
        Serial.print("DS18B20");
        break;
      case 0x22:
        Serial.print("DS1822");
        break;
      case 0x3B:
        Serial.print("DS1825");
        break;
      default:
        Serial.print("Unknown");
        break;
    }
    Serial.print(" temperature sensor: 0x");
    for (int i = 0; i < 8; i++)
    {
      if (deviceAddress[i] < 16) Serial.print("0");
      Serial.print(deviceAddress[i], HEX);
    }
    Serial.println("");
  }
  #endif
  
  // Set the WiFi pins (Needed by Adafruit Feather M0 WINC1500)
  //WiFi.setPins(8,7,4,2);
  
  // WiFi setup
  if (WiFi.status() == WL_NO_SHIELD) {                // check for the presence of the WINC1500
    #ifdef ENABLE_SERIAL
    Serial.println("WINC1500 not present! Nothing can be done!");
    #endif
    // don't continue:
    while (true);
  }
  #ifdef ENABLE_SERIAL
  Serial.println("WINC1500 Detected");
  
  // Display Firmware Version
  String fv = WiFi.firmwareVersion();
  Serial.print("  Firmware Version: ");
  Serial.println(fv);
  Serial.print("  Library Version: ");
  Serial.println(WIFI_FIRMWARE_LATEST_MODEL_B);
  #endif
        
  // Turn on WINC1500 WiFi module and connect to network now
  WiFi.begin(SECRET_SSID, SECRET_PASSWORD);

  // MQTT setup
  mqtt.setOptions(15*60, true, 5000);                 // keep Alive, Clean Session, Timeout
  mqtt.begin(MQTT_SERVER, MQTT_SERVERPORT, net);
  mqtt.onMessageAdvanced(messageReceived);
  
  #ifdef ENABLE_WATCHDOG
  // Set up the generic clock (GCLK2) used to clock the watchdog timer at 1.024kHz
  REG_GCLK_GENDIV = GCLK_GENDIV_DIV(4) |              // Divide the 32.768kHz clock source by divisor 32, where 2^(4 + 1): 32.768kHz/32=1.024kHz
                    GCLK_GENDIV_ID(2);                // Select Generic Clock (GCLK) 2
  while (GCLK->STATUS.bit.SYNCBUSY);                  // Wait for synchronization

  REG_GCLK_GENCTRL = GCLK_GENCTRL_DIVSEL |            // Set to divide by 2^(GCLK_GENDIV_DIV(4) + 1)
                     GCLK_GENCTRL_IDC |               // Set the duty cycle to 50/50 HIGH/LOW
                     GCLK_GENCTRL_GENEN |             // Enable GCLK2
                     GCLK_GENCTRL_SRC_OSCULP32K |     // Set the clock source to the ultra low power oscillator (OSCULP32K)
                     GCLK_GENCTRL_ID(2);              // Select GCLK2         
  while (GCLK->STATUS.bit.SYNCBUSY);                  // Wait for synchronization

  // Feed GCLK2 to WDT (Watchdog Timer)
  REG_GCLK_CLKCTRL = GCLK_CLKCTRL_CLKEN |             // Enable GCLK2 to the WDT
                     GCLK_CLKCTRL_GEN_GCLK2 |         // Select GCLK2
                     GCLK_CLKCTRL_ID_WDT;             // Feed the GCLK2 to the WDT
  while (GCLK->STATUS.bit.SYNCBUSY);                  // Wait for synchronization

  REG_WDT_CONFIG = 0xBu;                              // Set the WDT reset timeout to 16384 clock cycles or 16s seconds
  while(WDT->STATUS.bit.SYNCBUSY);                    // Wait for synchronization
  REG_WDT_CTRL = WDT_CTRL_ENABLE;                     // Enable the WDT in normal mode
  while(WDT->STATUS.bit.SYNCBUSY);                    // Wait for synchronization
  #endif

  // check connections
  connect();
}

// Arduino loop function
void loop() {
  static uint32_t lastDebounceTime[NUMBER_INPUTS] = {0, 0, 0, 0, 0, 0, 0, 0};
  static uint8_t  lastDebounceInput[NUMBER_INPUTS] = {-1, -1, -1, -1, -1, -1, -1, -1};
  static uint32_t lastTempUpdate = 0 - TEMP_RATE;     // used to measure the temp at a defined rate
  static uint32_t lastTempRequest = 0 - TEMP_RATE;    // used to delay the time between temp request and temp read
  static GateStateEnum curGateState = GS_RESET;       // current gate state for state machine
  static GateStateEnum nextGateState = GS_UNKNOWN;    // next gate state for state machine
  char            tempStr[16];                        // temporary string
  float           lastTemp;                           // last measured temperature
  uint8_t         inputReading;                       // last input read
  bool            inputStabilized = true;             // when true inputs are stabilized and are ready to be read
  
  // Reset the watchdog with every loop to make sure the sketch keeps running.
  watchdogReset();
  
  #ifdef ENABLE_OTA_UPDATES
  // check for WiFi OTA updates
  WiFiOTA.poll();
  #endif
  
  // MQTT client loop call
  mqtt.loop();
  
  // debounce input
  for (int i = 0; i < NUMBER_INPUTS; i++) {
    // read the current input state
    inputReading = digitalRead(input_pins[i]);
    // update last debounce time if the state has changed
    if (inputReading != lastDebounceInput[i]) {
      // reset the debounce timer
      lastDebounceTime[i] = millis();
    }
    // if debounce time has elapsed then the input is stable
    if ((millis() - lastDebounceTime[i]) > DEBOUNCE_TIME) {
      // debouced finished but update only if changed
      if (inputState[i] != inputReading) {
        // input actually changed, not updated with the same value
        inputState[i] = inputReading;                 // update input
      }
    }
    // last is now current
    lastDebounceInput[i] = inputReading;
  }
  
  // handle deactivating outputs
  for(int i = 0; i < NUMBER_OUTPUTS; i++) {
    if (outputState[i] == HIGH) {
      // output is currently active
      if ((millis() - lastOutputTime[i]) > CONTACT_TIME) {
        // output has been active long enough
        outputState[i] = LOW;                         // deactive output
        digitalWrite(output_pins[i], LOW);            // make output inactive
        digitalWrite(BOARD_LED, LOW);                 // deactivate visual indication
      }
    }
  }
  
  // handle deadband between output activations
  if (outputDeadband == HIGH) {
    // deadband is currently active
    if ((millis() - lastOutputDeadbandTime) > (CONTACT_TIME + CONTACT_DEADBAND_TIME)) {
      // deadband has been active long enough
      outputDeadband = LOW;                           // allow another output to go active
    }
  }
  
  // inputs must have stabilized before they are read for the first time
  for(int i = 0; i < NUMBER_INPUTS; i++) {
    // check input to see if it is still default
    if (inputState[i] == -1) {
      inputStabilized = false;
      break;
    }
  }
  
  // if inputs are stabilized then check inputs as normal
  if (inputStabilized) {
    // handle Gate State Machine
    switch (curGateState) {
      case GS_RESET:
        if ((inputState[CLOSE_LIMIT_SENSE] == HIGH) && 
            (inputState[OPEN_LIMIT_SENSE] == HIGH)) {
          // Error condition because gate is OPEN and CLOSED at the same time
          nextGateState = GS_ERROR;                   // switch to Error State
        } else if (inputState[CLOSE_LIMIT_SENSE] == HIGH) {
          // Gate is now Closed
          nextGateState = GS_CLOSED;                  // switch to Closed State
        } else if (inputState[OPEN_LIMIT_SENSE] == HIGH) {
          // Gate is now Open all the way
          nextGateState = GS_OPEN;                    // switch to Open State
        }
        break;
      case GS_ERROR:
        if ((inputState[CLOSE_LIMIT_SENSE] == HIGH) && 
            (inputState[OPEN_LIMIT_SENSE] == LOW)) {
          // gate is now closed 
          nextGateState = GS_CLOSED;                  // switch to Closed State
        } else if ((inputState[CLOSE_LIMIT_SENSE] == LOW) && 
                   (inputState[OPEN_LIMIT_SENSE] == HIGH)) {
          // gate is now closed 
          nextGateState = GS_OPEN;                    // switch to Open State
        }
        break;
      case GS_CLOSED:
        if ((inputState[CLOSE_LIMIT_SENSE] == HIGH) && 
            (inputState[OPEN_LIMIT_SENSE] == HIGH)) {
          // Error condition because gate is OPEN and CLOSED at the same time
          nextGateState = GS_RESET;                   // switch to Error State
        } else if (inputState[CLOSE_LIMIT_SENSE] == LOW) {
          // Gate is now Opening
          nextGateState = GS_OPENING;                 // switch to Opening State
        } 
        break;
      case GS_OPEN:
        if ((inputState[CLOSE_LIMIT_SENSE] == HIGH) && 
            (inputState[OPEN_LIMIT_SENSE] == HIGH)) {
          // Error condition because gate is OPEN and CLOSED at the same time
          nextGateState = GS_RESET;                   // switch to Error State
        } else if (inputState[OPEN_LIMIT_SENSE] == LOW) {
          // Gate is now Closing
          nextGateState = GS_CLOSING;                 // switch to Closing State
        }
        break;
      case GS_CLOSING:
        if ((inputState[CLOSE_LIMIT_SENSE] == HIGH) && 
            (inputState[OPEN_LIMIT_SENSE] == HIGH)) {
          // Error condition because gate is OPEN and CLOSED at the same time
          nextGateState = GS_RESET;                   // switch to Error State
        } else if (inputState[CLOSE_LIMIT_SENSE] == HIGH) {
          // Gate is now Closed
          nextGateState = GS_CLOSED;                  // switch to Closed State
        } else if (inputState[OPEN_LIMIT_SENSE] == HIGH) {
          // Gate is now Open
          nextGateState = GS_OPEN;                    // switch to Open State
        }
        break;
      case GS_OPENING:
        if ((inputState[CLOSE_LIMIT_SENSE] == HIGH) && 
            (inputState[OPEN_LIMIT_SENSE] == HIGH)) {
          // Error condition because gate is OPEN and CLOSED at the same time
          nextGateState = GS_RESET;                   // switch to Error State
        } else if (inputState[OPEN_LIMIT_SENSE] == HIGH) {
          // Gate is now Open
          nextGateState = GS_OPEN;                    // switch to Open State
        } else if (inputState[CLOSE_LIMIT_SENSE] == HIGH) {
          // Gate is now Closed
          nextGateState = GS_CLOSED;                  // switch to Closed State
        }
        break;
      default:
        // unknown state, force back to reset state
        nextGateState = GS_RESET;
        break;
    }
  }
    
  // Check connections
  if (!connect()) {
    // we are not currently connected, ignore rest of loop to prevent MQTT publishing
    // set Gate States so next loop will detect current Gate position
    //   and if connected will force a publish of Gate State
    curGateState = GS_RESET;
    nextGateState = GS_UNKNOWN;
    return;
  }
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

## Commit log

2018-05-18 Rename Arduino project. README updates. Added status section to software README.
2018-05-22 Still fixing errors in README's.
    [WiFi_Gate_Controller.ino]
2018-05-28 Update LED indication
    LED is turned on when a command input is active instead of command output. Fixed some compilere warnings.
    [WiFi_Gate_Controller.ino]
2018-05-31 Upped Version to 0.2. Added WiFi reconnect cycle. Added Print() and Println() defines. Watchdog Timeout changed.
    WiFi will now attempt a reconnect when it has been disconnected for too long. Println() and Print() defines embed the ENABLE_SERIAL define making code look cleaner. Watchdog Timeout set to 64 seconds from 16 seconds. MQTT keepalive interval changed to 65 seconds from 15 minutes. Reorganized code.
    [WiFi_Gate_Controller.ino]
2018-06-03 Cleanup ifdef ENABLE_SERIAL in program. Fixed temperature publishing to prevent a series of catchup publishes if the MQTT server was offline.
    [WiFi_Gate_Controller.ino]
2018-06-11 Upped version to 0.3. Improved WiFi reliablity.
    Sometime WIFi looses access to network without showing disconnected in status. To get around this timeout on MQTT connect retries was added. This stops the WiFi connection so it can reconnect.
    [WiFi_Gate_Controller.ino]
2018-06-12 Upped version to 0.3. Added automatic support for testing on other boards.
    Updated status in README.
2018-07-31 Update to KiCad 5.0.0. Remove unecessary files.
2019-03-03 Arduino IDE 1.8.8, updated WINC1500 firmware to 19.6.1.
2019-05-05 Update to KiCad 5.1 libraries.
    Also updated custom libraries.
    [WiFi-Gate-Controller-BOM.csv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]
2019-05-11 Remove unnecessary gerbers. Update gerber generation settings.
    [WiFi-Gate-Controller-B_Cu.gbl, WiFi-Gate-Controller-B_Mask.gbs, WiFi-Gate-Controller-B_SilkS.gbo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]
2019-05-21 Arduino library updates.
    Cleanup BOM.
    Support KiBom.
    [WiFi-Gate-Controller-BOM.csv, WiFi-Gate-Controller.kicad_pcb, WiFi-Gate-Controller.sch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]
2019-06-05 Minor formatting cleanup.
    [WiFi-Gate-Controller-BOM.csv]
2021-03-28 Add Home Assistant device support
    The Gate Controller will now show up as a device under mqtt integration. All entities will be associated with the device. Unique_id comes from SAMD21 processor serial.
2021-04-04 Revert to more stable code
    Recent changes to the add Home Assistant device information to the MQTT topics caused instability. This is probably related to String library usage. The changes that caused problems are now in the device branch. Master is back to previous stability but without device support.
    [WiFi_Gate_Controller.h, WiFi_Gate_Controller.ino]
2021-11-08 Update Kicad link.
